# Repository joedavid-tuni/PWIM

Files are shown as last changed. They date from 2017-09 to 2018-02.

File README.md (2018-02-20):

## ELECTRONIC CONTROL OF HYRDRAULIC SYSTEMS

## Description of the Task

As mobile equipment becomes more technologically sophisticated, the need for electronic control of
hydraulic systems is growing.

Electronic components have become more reliable and rugged. They can now withstand the harsh
environmental conditions required for mobile equipment applications. Sophisticated electronic
controllers normally supply only low power control signals.

The goal of the project is to build an electronic driver circuit that compensates the stiction and
hysteresis of a hydraulic valve that makes their behaviour seem erratic and unpredictable. Once we
get over these issues we move on to implement a current sensing mechanism by which the current
in the solenoid circuit is prevented from fluctuating due to varying resistance from varying
temperatures of the coil. We as such are not interested in the position of the spool at any given
point in time but rather only to regulate the current.

## Table of Contents

- Terms of Reference
- Abstract
- Acknowledgement
- 1. Introduction
   - 1.1 Hydraulic Valve
      - 1.1.1 Introduction
      - 1.1.2 Working Principle
      - 1.1.3 Solenoid
      - 1.1.4 Characteristics of Solenoid Coil
   - 1.2 Methods for Proportional Control
      - 1.2.1 Using a potentiometer in Series with the Solenoid
      - 1.2.2 Pulse Width Modulation
      - 1.2.3 Problems associated with Proportional Control of Solenoids
   - 1.3 Solutions to Problems associated with Proportional Control – The Concept of Dither
      - 1.3.1 High frequency PWM
      - 1.3.2 Low frequency PWM
      - 1.3.3 Superimposing Low Frequency Dither on High Frequency Signal
- 2. Current Sensing
   - 2.1 INA219
   - 2.2 PID Algorithm
- 3. Project Work
   - 3.1 Major Hardware Components
   - 3.2 Software
      - 3.2.1 Simulation
      - 3.2.2 Programming IDE
      - 3.2.3 PCB Design Software
   - 3.3 Project Implementation
      - 3.3.1 Basic Circuit
      - 3.3.2 Calculating Inductance
      - 3.3.3 Dither
      - 3.3.4 Current Sensing
      - 3.3.5 Making the PCB
- 4. Project Setup
- 5. Conclusion
- 6. Project Resources
- 7. References
- APPENDIX A: I^2 C Communication Protocol
- APPENDIX B: Setting PWM Frequency on Arduino
- APPENDIX C: The PID Algorithm
- APPENDIX D: TROUBLESHOOTING
- Figure 1: Parts of the Hydraulic Valve List of Figures
- Figure 2: Internal cross section of the Hydraulic Valve
- Figure 3: Coil of Solenoid A energized
- Figure 4: Neutral Position of Valve Plunger
- Figure 5: Testing using mechanical override
- Figure 6: Cross-sectional sketch of Solenoid A of hydraulic valve
- Figure 7: Depiction of the magnetic field around solenoid
- Figure 8: Solenoid current characteristics
- Figure 9: Width of pulses at different duty cycles
- Figure 10: Duty cycle with respective current waveform
- Figure 11: A typical hysteresis curve in an electro hydraulic proportional valve
- Figure 12: Dither as a by-product of low frequency PWM
- Figure 13: Low Frequency Dither superimposed on high frequency PWM
- Figure 14: Functional block diagram of commercially available Solenoid Driver
- Figure 15: Dither Generating Circuitry of a commercially available driver
- Figure 16: Software Code for creating Dither
- Figure 17: Functional Block Diagram of INA219 Sensor
- Figure 18: LCD Display used in the project
- Figure 19: Screenshot of Multisim GUI
- Figure 20: Screenshot of Labcenter Proteus GUI
- Figure 21: Screenshot of Arduino IDE GUI
- Figure 22: Screenshot of Autodesk Eagle GUI
- Figure 23: An FET and a freewheeling diode used to drive the solenoid valve.
- Figure 24: Laboratory setup while calculating inductance
- Figure 25: Oscilloscope Screenshot at resonance
- Figure 26: Multisim simulation circuit
- Figure 27: Breadboard schematic
- Figure 28: General Schematic
- Figure 29: Simulated oscilloscope screenshot (Low frequency)
- Figure 30: Project Implementation waveform from the Arduino (Low frequency)
- Figure 31: Simulated oscilloscope screenshot (High frequency)
- Figure 32: Project Implementation waveform from the Arduino (High frequency)
- Figure 33:: Project Implementation of superimposed waveform from the Arduino.
- Figure 34: Breadboard schematic for current sensing
- Figure 35: Project implemented waveform from the Arduino with current sensing incorporated
- Figure 36: Schematic of Printed Circuit Board of Valve Driver Circuit
- Figure 37: Board Layout of Printed Circuit Board of Valve Driver Circuit
- Figure 38: 3D rendered images of designed Printed Circuit Board
- Figure 39: 3D rendered images of designed Printed Circuit Board
- Figure 40: 3D rendered images of designed Printed Circuit Board
- Figure 41: 3D rendered images of designed Printed Circuit Board
- Figure 42: Project Setup

## 1. Introduction

### 1.1 Hydraulic Valve

#### 1.1.1 Introduction

The Hydraulic Valve used for this Project is a bi-directional solenoid valve from BOSCH.

These are designed to perform any of three actions. They direct the flow of fluid in a hydraulic
system in a particular direction. They can halt or initiate the flow of fluid in a system. Directional
valves can also change the direction in which a fluid flows within a circuit. Various directional valves
are incorporated in hydraulic systems to enable proper flow of fluids. Spool valves in particular are
designed to block and allow the flow of fluid within a hydraulic system.

Parts of the Hydraulic Valve (as labelled in Figure 1)

1. 3 port/chamber system with spool guidance
2. Pressure tight solenoid
3. Optimized flow paths
4. Manual override with return spring

#### Figure 1 : Parts of the Hydraulic Valve

<a href="https://drive.google.com/uc?export=view&id=103Zk_Gb4QrChb2lCu6mXjAdsSugn9ifj">Click for the larger version.</a>

#### 1.1.2 Working Principle

#### Figure 2: Internal cross section of the Hydraulic Valve

<a href="https://drive.google.com/uc?export=view&id=1MhIU9a9HzgaAY-1frNQojasQYRDYau8C">Click for the larger version.</a>

The valve contains two coils on its either end and together with the valve tube that contains an  armature and a push pin make up what is known as a solenoid.

In the main body of the valve there are two springs that help return the spool when no solenoids are
energized. The lines with the gauges labelled A and B are the work ports that typically connect to a
hydraulic cylinder or a motor.

When Solenoid A of the valve is energized an electromagnetic field is created (Figure1). The field
pulls the armature in towards the centre of the winding which causes the armature to slide easily in
a tube that is internally lubricated with hydraulic oil. The armature moves the push pin and
ultimately the push pin moves the valve spool towards the right and now there will be a flow from
the pump directed to work port B. Likewise when Solenoid B is energized, the spool moves to the
left.

#### Figure 3: Coil of Solenoid A energized

<a href="https://drive.google.com/uc?export=view&id=1noz2zwyRv9kF4yIksqgTtab-pTfS3ick">Click for the larger version.</a>

Notice that when Solenoid A is energised the movement of the spool towards the right also causes
the pushpin and armature in Solenoid B is pushed to the right as well.

Also notice that in Figure 2 there is a gap present between the pushpin on the left side of the spool.
When Solenoid A is energized the armature and the push pin gets a running start against the spool
as the gap is closed.

When the solenoid returns to the neutral position after Solenoid A is energized the gap is present
with the Solenoid B. Whichever side of the valve has the pushpin gap has a slight force advantage
when that Solenoid is next energized (Figure 4 ).

#### Figure 4: Neutral Position of Valve Plunger

<a href="https://drive.google.com/uc?export=view&id=1vX9gAe1uKFn87bVOUZPevz9T227o3frZ">Click for the larger version.</a>

In order to help with troubleshooting and basic valve testing, the valve is provided with a mechanical
override (Figure 5), A mechanical override is simply a pin on the outside end of the valve tube in the
centre of the solenoid assembly that can be activated with a small screwdriver or hex key. Pushing
on the mechanical override is a simple way to find out if the internal parts of the valve is still free to
move and operating normally.

#### Figure 5: Testing using mechanical override

<a href="https://drive.google.com/uc?export=view&id=1xGuQGBYz5f1ClA1LN9TVYjQGVeLfPqYV">Click for the larger version.</a>

#### 1.1.3 Solenoid

The hydraulic solenoid valve as mentioned has two solenoids as actuators mounted on either ends
of the valve body. These linear solenoids are electromechanical devices which convert electrical
energy into a linear mechanical motion which is used to control the hydraulic system.
Figure 6 shows a cross sectional sketch of the electromagnetic solenoid hydraulic valve. The
solenoids consist of an electromagnetically inductive coil wound around a movable armature, or
plunger. The coil is shaped such that the armature can be moved in and out of its centre, altering the
coil’s inductance. The plunger provides mechanical force to activate the control mechanism, for
example opening and closing of a valve.

#### Figure 6: Cross-sectional sketch of Solenoid A of hydraulic valve

<a href="https://drive.google.com/uc?export=view&id=1pHDuV0NiXC4nKBy8d_73bMfwTTyaZYxM">Click for the larger version.</a>

#### 1.1.4 Characteristics of Solenoid Coil

A main electrical characteristic of a solenoid is that of an inductor that opposes any change in
current. This characteristic is why current does not immediately reach a maximum level when a
solenoid is energized. Instead, the current rises at a steady rate until it is limited by the DC resistance
of the solenoid.

#### Figure 7: Depiction of the magnetic field around solenoid

<a href="https://drive.google.com/uc?export=view&id=10Lr9DRpki1RoA1x1QTP7i0Ylmb1DseCf">Click for the larger version.</a>

An inductor (in this case a solenoid) stores energy in the form of a concentrated magnetic field.
Whenever current is present in a wire or conductor, a magnetic field, however small, is created
around the wire. With the wire wound into a coil, such as in the solenoid, the magnetic field
becomes very concentrated. This electromagnet can control a mechanical valve through an electrical
signal.

As soon as the solenoid is energized, the current increases, causing the magnetic field to expand
until it becomes strong enough to move the armature and the corresponding solenoid current is
known as IPEAK.

#### Figure 8: Solenoid current characteristics

<a href="https://drive.google.com/uc?export=view&id=1ldvCfLj_Tx2C3A3EPOGBCEJUdh6es91O">Click for the larger version.</a>

The armature movement increases the concentration of the magnetic field as the armature’s own
magnetic mass moves farther into the magnetic field. Remember, a magnetic field changing in the
same direction of the current creating it induces an opposing voltage into the windings. Because the
magnetic field quickly expands when the armature strokes, the field causes a brief reduction in the
current through the solenoid windings till a minimum known as IVALLEY (Figure 8). Notice the
prominent dip in the rising portion of the current waveform.

After the armature strokes, the current continues on its normal upward path to its maximum level. A
typical current waveform in shown in Figure 8.

### 1.2 Methods for Proportional Control

When voltage is applied to a valve coil, the current flowing through it creates a magnetic field which
provides the force to shift the valve’s spool. The input voltage divided by the resistance of the coil
equals the current draw. This is very straightforward when used with on/off valves, but proportional
valves are only useful if the spool position can be precisely controlled by varying the input current.

#### 1.2.1 Using a potentiometer in Series with the Solenoid

A simple potentiometer can be used to vary the resistance, which then varies the input current. This
is an inefficient method of control, and is not practical when high currents are required. Also, when
an infinitely variable DC signal is used to operate a proportional valve solenoid, the output transistor
functions like a variable resistor. It drops the power supply voltage down to the level required by the
solenoid coil at a particular time. The full coil current, which may be several amps, needs to pass
through this output transistor. The result is that the transistor builds up heat which requires a large
heat sink to dissipate.

#### 1.2.2 Pulse Width Modulation

Pulse Width Modulation (PWM) is a control technique which can overcome the problems described
above. With PWM, the output transistor is used as an on/off switch, feeding the solenoid coil with a
series of on/off pulses at a constant voltage. The pulses are set at a constant frequency, typically 400
to 5000+ Hz. The signal level is determined by varying the duration of the “on” pulses relative to the
“off” pulses.

The advantage of this technique is that during the “off” pulse, the output transistor is not passing
any current, and during the “on” pulse, there is virtually no voltage drop across the transistor and
therefore very little heat is created. In practice, there will be a small voltage drop across the
transistor during the “on” pulses, and it takes a finite amount of time to switch on and off, so a small
amount of heat is created. However, the amount of heat is much smaller than would be produced by
a conventional DC output signal.

PWM has become the standard for all valve amplifiers in order to reduce amplifier size and power
waste. No modifications are required to the valve solenoid in order to use this technique.

PWM is an efficient way to control current to a proportional valve coil. It allows the use of
electronics for current regulation, dither, ramping, short circuit protection, and the elimination of
deadband.

**How PWM Works**

A PWM signal is not constant, it is on for a period of time and off for a period of time (see Figure 9 ).

#### Figure 9: Width of pulses at different duty cycles

<a href="https://drive.google.com/uc?export=view&id=1Hj7wRIMUwGXi5BsZQd7tWuWXpfzszCKg">Click for the larger version.</a>

The duty cycle “D” refers to the “on” portion of the cycle. The duty cycle can be anywhere from 0
(signal always off) to 1 (signal always on). A 50% “D” results in a perfect square wave.

Inductance is the characteristic of a circuit that opposes the starting, stopping or changing of current
flow. Inductance in an electrical system is similar to inertia in a mechanical system. Its effect is to
introduce a time lag into the duty cycle wave form. In theory, the wave form is perfectly rectangular,
rising immediately when current is applied, and falling immediately when current is withdrawn.
Because of the effects of inductance, the actual wave form rises and falls more gradually (see Figure
10 ).

#### Figure 10: Duty cycle with respective current waveform

<a href="https://drive.google.com/uc?export=view&id=1ye-VUofCY1JmQrYZPyqtdv7DvxmzGXA0">Click for the larger version.</a>

At 25% signal, “D” is shorter than the time it takes the current to reach its maximum value. This
results in reduced current output to the valve coil, and therefore a reduced hydraulic output from
the valve. If the PWM frequency is low enough, the current will fall to zero during the off time. This
is described as “discontinuous current.”

#### 1.2.3 Problems associated with Proportional Control of Solenoids

There are two major problems that are associated with basic proportional control of solenoid.

1. Stiction

Stiction keeps the valve spool from moving when input signal changes are small. When the signal
finally becomes large enough to initiate movement, the spool will tend to overshoot the position
required for accurate control.

2. Hysteresis

#### Figure 11: A typical hysteresis curve in an electro hydraulic proportional valve

<a href="https://drive.google.com/uc?export=view&id=1HjYDC2TtLQYjVnxpmJmntj7FKT0Biom-">Click for the larger version.</a>

The spool movement in a proportional valve has to overcome some amount of spring force as well
as static friction when the input signal is applied. These forces produce an effect known as
hysteresis. Additionally, the solenoid has to overcome the magnetic hysteresis due to the cyclic
magnetization and demagnetization of the solenoid core. The spool movement in response to the
increasing input signal is not the same as the spool movement created in response to the decreasing
input signal. Hysteresis as shown in the figure above is defined as the difference in the spool position
produced by a particular input signal when it is increasing and then decreasing.

Stiction and hysteresis can make the behaviour of a hydraulic proportional valve seem erratic and
unpredictable. In the following sections, we will see how to overcome these problems.

### 1.3 Solutions to Problems associated with Proportional Control – The Concept of Dither

Dither is a rapid, small movement of the spool around the desired position. It is intended to keep the
spool moving to avoid stiction and average-out hysteresis. Dither amplitude must be **large enough
and the frequency slow enough for the spool to respond, and yet amplitude small and frequency
fast enough to avoid creating a noticeable pulsation in the hydraulic output of the valve.** Dither is
caused by coil current “ripples”—current variations around the desired control signal value. Due to
inertia, the valve spool will follow low frequency ripples better than it will follow high frequency
ripples. The amplitude of the ripples determines if, or how far, the spool will move at a given
frequency.

#### 1.3.1 High frequency PWM

The solenoid valves are very often operated by means of PWM signals at a frequency that is high for
the solenoid valve, for example at l KHZ, in the linear or analog range. The armature of the solenoid
valve cannot synchronously follow this high control frequency in mechanical terms and assumes an
intermediate position.

#### 1.3.2 Low frequency PWM

Previously these problems Were solved in that the frequency of the control signal has been reduced
to such an extent, for example between 70 - 300 HZ, that the armature can still just about follow and
in the intermediate position or central position is preferably deflected only minimally. This results in
oscillation of the armature, and of the valve connected thereto, about the intermediate position at
low amplitude which is conventionally called dither oscillation (dither signal). This dither oscillation is
desired in principle since the friction resistances at the moving parts of the solenoid valve may be
reduced thereby.

However, it is very difficult to stipulate an optimally constant dither signal amplitude **since the
dither signal depends on the PWM frequency and on the pulse-duty factor (duty cycle)** and
therefore on the coil current flowing in the solenoid valve. With this method, it is therefore **not
possible for the dither signal to form a constant amplitude since the PWM frequency has to be
continuously adjusted as a function of the stipulated desired current value and in the process the
amplitude and the frequency of the dither signal change accordingly.**

#### Figure 12: Dither as a by-product of low frequency PWM

<a href="https://drive.google.com/uc?export=view&id=1ios9JTr9PqKZaDLKV-OdVEeYfnglZrMP">Click for the larger version.</a>

#### 1.3.3 Superimposing Low Frequency Dither on High Frequency Signal

A further solution for said problems consists in a low-frequency dither signal being superimposed on
the high frequency of the PWM signal by amplitude modulation. This allows the user to
**independently control** amplitude and frequency of the **solenoid current** and the **dither**. The dither
will therefore be constant for any current level, and its frequency and amplitude can be set by the
user to optimize the function of the particular hydraulic valve. This will be necessary as different
valves from different manufacturers would have different spool dynamics (inertia due to different
size, for example).

#### Figure 13: Low Frequency Dither superimposed on high frequency PWM

<a href="https://drive.google.com/uc?export=view&id=1-vaZGm2uEeG3nVKuvEL_0PmVU9jZDm8H">Click for the larger version.</a>

The dither is specified by its frequency (Hz) and peak-to-peak current. The dither amplitude is usually
adjustable from 0 to 10% of the rated maximum current of the solenoid.

It is to note that, if the dither frequency is in the range of the control frequency, undesirable low-
frequency beating of the magnetic current can occur. Even the hydraulic system may be damaged
thereby. The beating results because the dither frequency cannot be synchronized with the control
frequency.

**Hardware Techniques**

Most solenoid valve drivers make use of a separate dither generating circuitry and combines it with
the main PWM signal using op-amps. The functional block diagram of one such driver is as shown in
the figure below:

#### Figure 14: Functional block diagram of commercially available Solenoid Driver

<a href="https://drive.google.com/uc?export=view&id=1qd2-SRFe5xwFcBycASi99DSaOHfmeA4B">Click for the larger version.</a>

A dither generating circuit of a commercially available solenoid driver is shown below. This is capable
of generating triangular and square wave dither.

#### Figure 15: Dither Generating Circuitry of a commercially available driver

<a href="https://drive.google.com/uc?export=view&id=1yqVyhJahEJyZMxh-2SUGGK5sMoNQTPDx">Click for the larger version.</a>

Working principle:

The dither generator consists of a comparator stage (A1A), amplitude limiting stages (A1C/D2 AND
A1D/D1) and an integrating amplifier stage (A1B). In the beginning, A1A will attempt to go to
positive or negative saturation. However, the peak voltage will be restricted by D1/A1D or D2/A1C.
A1B ramps up or down, as whatever the case maybe, until the output voltage is sufficient to cause
the feedback voltage at the comparator (through voltage divider R8, R11) to change polarity. At this
point, the polarity of A1A changes and A1B ramp in the opposite direction. This way, the dither
signal is generated.

Solutions of this nature are cost-intensive.

**Software Technique**

For the context of the project, we focus only on
superimposing the dither on main PWM signal. As
such, the requirements are basic and we do not need
sophisticated electronics for the purpose. All the
hardware needed would be the basic hardware for
the PWM switching of the solenoid and the dither can
be implemented without using the dither circuitry buy
by rather manipulating the switching hardware
through the software. This section is a description of
how it is done.

#### Figure 16: Software Code for creating Dither

<a href="https://drive.google.com/uc?export=view&id=17Wmvigc5C_fGLL_dgWxXKkvWKsJW3kRq">Click for the larger version.</a>

Using software, the microcontroller is programmed so that the duty cycle of the PWM is periodically
oscillated about its set setpoint, by the dither amplitude which in “duty-cycle language” is in effect a
small finite amount of pulse-duty factor. This in effect causes an extended and thereafter a
shortened PWM signal cyclically which emulates dither. This way, the pulse-duty factor is changed
by the desired amplitude of the dither signal exactly every consequent cycle.

A constant amplitude for the dither signal may advantageously be formed thereby, so the armature
of the solenoid valve always oscillates about its central position with identical excursions, without
the control frequency of the PWM signal being able to have an adverse effect. The resulting reduced
friction resistance therefore allows the position of the armature to be advantageously adjusted and
controlled much more accurately as discussed earlier

The low frequency of the dither signal means that the oscillation of the solenoid valve armature can
be individually adjusted to the type of solenoid valve being used, so, compared with the known
hardware solution, a high level of flexibility results because the adaptation to other types of solenoid
valve can take place by way of a simple calibration process by changing a value in the code that the
microcontroller uses to generate the dither. It is also cost efficient in terms of the components used
as the dither circuitry is now replaced by software code.

## 2. Current Sensing

As mentioned in the previous section, the armature of a solenoid provides a mechanical force to
activate the control mechanism. The force applied to the armature is proportional to the coil’s
change in inductance with respect to the armature’s change in position. The electromagnetic force
of a solenoid directly relates to the current. Traditionally, a voltage drive powers the solenoid coils;
Therefore, the coil consumes a continuous power. A negative effect of this power consumption is
the heating of the coil. The coil temperature is a result of many factors: ambient temperature, self-
heating due to the coil’s power consumption (V × I), heating induced by the contact system, and
other heat sources such as components in the vicinity of the relay. Due to coil heating, the coil
resistance increases. The resistance at elevated temperature is expressed by Equation:

where

- RCoil_20°C is the 20°C value for resistance
- kR_T is the thermal coefficient of copper (= 0.00404 per °C) (1)

Typically given in the datasheet of a solenoid coil, RCoil_20°C can calculate the worst-case coil
resistance at high temperatures.

To compensate for temperature induced changes, we have to implement some sort of current
sensing algorithm which essentially is a current feedback. This allows the solenoid current to be
proportional to the input signal voltage, and independent of the solenoid resistance. Power supply
voltage must be sufficient to overcome the increased or decreased resistance

### 2.1 INA219

The current sensor used for the project is the INA219.

The two analog inputs to the INA219, IN+ and IN–, connect to a shunt resistor in the bus of interest.
The INA219 is typically powered by a separate supply from 3 to 5.5 V. The INA219 senses the small
op across the shunt for shunt voltage, and senses the voltage with respect to ground from IN– for
the bus voltage. Figure 13 shows this operation

#### Figure 17: Functional Block Diagram of INA219 Sensor

<a href="https://drive.google.com/uc?export=view&id=1i2oJyiAauu5uhqEkzyX2_yDP42nBgh-j">Click for the larger version.</a>

### 2.2 PID Algorithm

The PID Controller is implemented to achieve the current sensing functionality. See APPENDIX C: The
PID Algorithm to see the details of the PID Algorithm.

The PID algorithm consists of three basic coefficients; proportional, integral and derivative which are
varied to get optimal response. The basic idea behind a PID controller is to read the values from the
current sensor, then compute the desired actuator output by calculating proportional, integral, and
derivative responses and summing those three components to compute the output.

**Proportional Response:** The proportional component depends only on the difference between the
set point and the process variable. This difference is referred to as the Error term. The proportional
gain (Kp) determines the ratio of output response to the error signal. Increasing the proportional
gain will increase the speed of the control system response. However, if the proportional gain is too
large, the process variable will begin to oscillate. If Kp is increased further, the oscillations will
become larger and the system will become unstable and may even oscillate out of control.

**Integral Response:** The integral component sums the error term over time. The result is that even a
small error term will cause the integral component to increase slowly. The integral response will
continually increase over time unless the error is zero, so the effect is to drive the Steady-State error
to zero. Steady-State error is the final difference between the process variable and set point. A
phenomenon called integral windup results when integral action saturates a controller without the
controller driving the error signal toward zero.

**Derivative Response:** The derivative component causes the output to decrease if the process
variable is increasing rapidly. The derivative response is proportional to the rate of change of the
process variable. Increasing the derivative time (Td) parameter will cause the control system to react
more strongly to changes in the error term and will increase the speed of the overall control system
response. Most practical control systems use very small derivative time (Td), because the Derivative
Response is highly sensitive to noise in the process variable signal. If the sensor feedback signal is
noisy or if the control loop rate is too slow, the derivative response can make the control system
unstable

**Tuning**

The method used for tuning the PID Controller in this project is the “trial and error” method.

In this method, the I and D terms are set to zero first and the proportional gain is increased until the
output of the loop oscillates. As one increases the proportional gain, the system becomes faster, but
care must be taken not make the system unstable.

Once P has been set to obtain a desired fast response, the integral term is increased to stop the
oscillations. The integral term reduces the steady state error, but increases overshoot. Some amount
of overshoot is always necessary for a fast system so that it could respond to changes immediately.
The integral term is tweaked to achieve a minimal steady state error.

Once the P and I have been set to get the desired fast control system with minimal steady state
error, the derivative term is increased until the loop is acceptably quick to its set point. Increasing
derivative term decreases overshoot and yields higher gain with stability but would cause the system
to be highly sensitive to noise.

## 3. Project Work

### 3.1 Major Hardware Components

<a href="https://drive.google.com/uc?export=view&id=1NwfCsXLhD1eqSOyNHsD_ij0nW3hgjotf">Click for the larger version.</a>

**Arduino**

The Arduino Uno is a microcontroller board based on the
ATmega328. Arduino is an open-source, prototyping
platform. The Arduino Uno has 14 digital input/output
pins (of which 6 can be used as PWM outputs), 6 analog
inputs, a 16 MHz crystal oscillator, a USB connection, a
power jack, an ICSP header, and a reset button. It
contains everything needed to support the
microcontroller; simply connect it to a computer with a
USB cable or power it with a AC-to-DC adapter or battery
to get started.

Features of the Arduino UNO:

- Microcontroller: ATmega328
- Operating Voltage: 5V
- Input Voltage (recommended): 7-12V
- Input Voltage (limits): 6-20V
- Digital I/O Pins: 14 (of which 6 provide PWM output)
- Analog Input Pins: 6
- DC Current per I/O Pin: 40 mA
- DC Current for 3.3V Pin: 50 mA
- Flash Memory: 32 KB of which 0.5 KB used by bootloader
- SRAM: 2 KB (ATmega328)
- EEPROM: 1 KB (ATmega328)

## • Clock Speed: 16 MHz

We use the Arduino to create the appropriate PWM signals for controlling the voltage to the
solenoid and to implement the algorithm for current sensing.

**Bidirectional Hydraulic Vale**

Manufacturer: Bosch Rexroth (BRH)

Part No.: 0810091203

Solenoid Specs:

Rating: 24V, 1.4A

**Power Supply**

Specs:

Rating: 24V,2.5A

**INA219, Bidirectional Current/Power Monitor with I2C Interface**

The INA219 is current shunt and power monitor with and I^2 C
interface. This along with the fact that it could be wired on the high
side were the prime reasons the device was selected to be used with
the I2C compatible Arduino.

The device is capable of monitoring both shunt voltage and the bus
supply voltage. The device uses a 3-5V supply, drawing a maximum of 1 mA of supply current and
operates from -40°C to 125°C.

**16x4 Liquid Crystal Display.**

A 16x4 LCD Display is used to display the circuit parameters such as duty cycle, current, etc. real
time.

The parameters on Display are:

Line 1: Duty cycle (Range: 0- 100 , from setpoint) Voltage: Voltage of the Solenoid Circuit
Line 2: I1 : Current sensed by the I2: Expected Current from duty cycle
current sensor (Feedback for PID)
Line 3: Power: VI Power Dissipated in the Solenoid Circuit
Line 4: PID constants (Kp, Ki, Kd)

#### Figure 18: LCD Display used in the project

<a href="https://drive.google.com/uc?export=view&id=1-ABclzSzZyn64kzNVGeBQozGHO7Giizi">Click for the larger version.</a>

**Other Electrical Components**

<a href="https://drive.google.com/uc?export=view&id=1LpvatdVxXZvamxfx_jg-BhqFKHSA1nNc">Click for the larger version.</a>

```
Device Part No. Rating Quantity Remarks
FET IRF3205PbF VDSS = 55V, ID = 110A (n-Ch) 1 Switching Device
Capacitor .001K 63 100nF 1 Noise Filter
Resistor - 12Ω 1 Current Limiter
Diode 1N5400 3A, Rectifier Diode 1 Freewheeling Diode
Potentiometer/
Joystick
```
- 10KΩ 1 Input to the System

### 3.2 Software

#### 3.2.1 Simulation

National Instruments, Multisim v12.0 (used for simulating electrical characteristics)

#### Figure 19: Screenshot of Multisim GUI

<a href="https://drive.google.com/uc?export=view&id=1yDhkocze4_SoT9yiW1kYx1o0pmJ9QOiR">Click for the larger version.</a>

LabCenter, Proteus 8 (used for simulating arduino microcontroller (with code) with electrical circuit)

#### Figure 20: Screenshot of Labcenter Proteus GUI

<a href="https://drive.google.com/uc?export=view&id=1wienvCHE1-AMao52zff7h7abuAwJmdlY">Click for the larger version.</a>

#### 3.2.2 Programming IDE

##### ARDUINO IDE

#### Figure 21: Screenshot of Arduino IDE GUI

<a href="https://drive.google.com/uc?export=view&id=177bdEXaEHLrz7efpmUK4lLl1IIjE5Dey">Click for the larger version.</a>

#### 3.2.3 PCB Design Software

#### Figure 22: Screenshot of Autodesk Eagle GUI

<a href="https://drive.google.com/uc?export=view&id=1jIhEK4rQlFEAy6yMQ-lyjC428kQFLo-f">Click for the larger version.</a>

### 3.3 Project Implementation

Before the implementation, the circuit needs to be simulated to study the response of the
circuit beforehand so that time is no wasted during implementation stage. An added benefit would
be familiar results and pre-known reasoning during the implementation phase. As mentioned in the
earlier sections we use MultiSim v12.0 and Proteus 8.0 for simulations. Proteus simulations were
made to study the behaviour while designing the project work and its observations are not recorded
here.

#### 3.3.1 Basic Circuit

Driving a solenoid is a rather simple task with very little need for sophisticated electronics. Still, the
basics of inductive load driving must be taken care of if we are to safely actuate this load. These
requisites are:

- A large enough voltage must be applied across the winding in order to supply a current with
    enough magnitude as to push/pull the piston.
- The switch or power stage must be sized according to the dc current we expect to see
    flowing across the solenoid winding.
- An alternate path must be applied to take care of the flowing current once the switching
    element is disabled.

A normal MOSFET requires around 10V applied to the Base pin to fully turn on. Because driving
anything above 5V with an Arduino requires using a level-shifter or amplifier, we use what is called a
logic-level MOSFET (IRF 3205) for direct integration. A logic-level MOSFET can be turned on with a 5v
“logic level” signal, which can be easily interfaced to the Arduino.

If a normal MOSFET with an amplified input from the Arduino is used, care must be taken not to
exceed the maximum gate-to-source voltages. If the limit is exceeded for even a second, it can
destroy the MOSFET, so care should be taken to work within the voltage limits of the MOSFET. The
maximum voltage that can be applied to the gate pin is listed in the datasheet as the “Gate to Source
Voltage” or “Vgs” —this number is usually between 18vdc and 25vdc.

For the IRF 3205 we the maximum Vgs is 20V, so it is safe as the Arduino cannot prover over 5V with
direct integration.

The typical solenoid driver circuit is a single FET transistor with enough current handling capability to
drive the load (IRF 3205), and a freewheeling diode which is forward biased when the FET is
disabled. When the FET is enabled, it sinks all the current needed to polarize the inductor. When the
transistor is disabled, the current flowing through the inductance must be allowed to decay down to
zero. The freewheeling diode is forward biased taking this current and avoiding damage to the
power FET. Figure 1 9 shows the two possible states a solenoid will experience as it is energized

#### Figure 23: An FET and a freewheeling diode used to drive the solenoid valve.

<a href="https://drive.google.com/uc?export=view&id=1sQTFtrDf82s8IXWCDfRFEJ_FRTnlli9v">Click for the larger version.</a>

Note that a H-bridge circuit is not used as it’s not a bistable solenoid where the direction of motion
is according to the magnetic field polarity. Hence the direction of current flow is not relevant and
use of an H-bridge would be an overkill as it would need 4 FETs as opposed to one in this case.

All information required to begin simulations is present except one, the inductance of the solenoid
of the hydraulic valve. This was neither found in the product datasheet nor was available with the
Bosch Customer Service personnel on contacting them. So, a basic test is carried out to approximate
the inductance of the solenoid.

#### 3.3.2 Calculating Inductance

To calculate the inductance, connect the solenoid of the hydraulic valve in parallel with a capacitor
to form a tank circuit. Use a function generator to run a small current through the circuit and an
oscilloscope to view the waveform across the solenoid. Next, sweep the function generator
frequency from its lowest top highest range. In this range, the tank's resonant frequency is where
the oscilloscope registers the largest waveform.

#### Figure 24: Laboratory setup while calculating inductance

<a href="https://drive.google.com/uc?export=view&id=1DbEUsarPM3vBnsaWHENC6-nMKgTmmU00">Click for the larger version.</a>

Resonant Frequency of LC tank circuit is given by the formula:

##### 푓=

##### 1

##### 2 휋√퐿퐶

Equation 1

From the equation 1 the inductance can be found, L, as:

##### 퐿=

##### 1

##### ( 2 휋푓)^2 .퐶

Equation 2

Resonance was found to obtained at around 150Hz using
a capacitor of 10μF.

Substituting in Equation 2, the inductance,

```
L= 0.10554 H or 105.54mH
```
#### 3.3.3 Dither

Now, that the inductance of the solenoid is established, it is simulated in softwares. Next,
simulations at both higher and lower frequencies is carried out and the observations are recorded
below.

**Simulation Circuit**

The circuit built is shown in the figure below.

As can be seen the **voltage across the solenoid is connected to channel A** and **the current in the
solenoid is connected to channel B** of the oscilloscope.

#### Figure 25: Oscilloscope Screenshot at resonance

<a href="https://drive.google.com/uc?export=view&id=1k7YGEA7DGEtcj9yKaFBfLAySiLHO5YZx">Click for the larger version.</a>

#### Figure 26: Multisim simulation circuit

<a href="https://drive.google.com/uc?export=view&id=1Tc4o473i5xGG8D_BdxKo3akBl32X1_w4">Click for the larger version.</a>

**Arduino Valve Driver Circuit**

#### Figure 27: Breadboard schematic

## Figure 28: General Schematic

The PWM frequency on most pins is ~490 Hz. However, it's ~980 Hz for pins 5 and 6 on the Uno. To
obtain lower frequencies a deeper understanding on the hardware implementation of the ATMEL
328p Microprocessor that the Arduino uses is necessary.

See APPENDIX B: Setting PWM Frequency on the Arduino to see how a frequency different from that
of the default frequency was obtained.

Also see APPENDIX D: Troubleshooting to see how to eliminate noises in the analog input

The waveforms from the scope are shown in the figure below.

**Low Frequency Dither Observations**

(refer Section 2.3.2 for literature)

Frequency: ( 60 Hz) and PWM with
duty cycle: 80%

**Simulation Results:**

## Figure 29: Simulated oscilloscope screenshot (Low frequency)

As described in Section 2.3.2, low frequency PWM generates dither (current ripple) as a by-product
of the PWM process. The PWM frequency is low enough so that the current has time to decay
before the next rise begins.

**Project Implementation Results**

## Figure 30: Project Implementation waveform from the Arduino (Low frequency)

The above is a plot of instantaneous values of the current (Y-axis) vs time (x-axis) that that micro-
controller records. The blue is the expected current value at 80% duty cycle whereas the redline is
the current values sensed by the sensor in the feedback circuit. It is observed that the frequency of
the PWM is low enough that it reduces to 0 at moments. This is in line with what was expected and
as shown in the simulations

**Valve Behaviour**

As the duty cycle was increased, the plunger of the solenoid began to vibrate with larger amplitude
and finally actuated. This was as expected as mentioned in the Section 2.3.2. Changing the PWM
frequency will allow adjusting the dither, but the amplitude and frequency of the dither cannot be
set independently.

**Results from Test Bench.**

Due to large hysteresis of the solenoid used in the test bench, the dither could be observed in the
initial stages for a brief amount of time but it quickly actuated.

**High Frequency Dither Observations**

(refer Section 2.3.1 for literature)

**Simulation Results:**

Frequency: ( 490 Hz – Arduino Default frequency) and PWM with
duty cycle: 80%

## Figure 31: Simulated oscilloscope screenshot (High frequency)

Here, it is clear that the frequency of the PWM signal is high enough that it does not let the current
to a minimum zero value.

**Valve Behaviour**

The armature of the solenoid valve cannot synchronously follow the current in mechanical terms
and assumes an intermediate position. With a pulse duty factor of 50% of the PWM signal this then
corresponds to the central position of the valve “half open”. But this as discussed in Section 2 .3.1
will be subject to problems of stiction and thereby hysteresis due to lack of dither oscillation.

**Project Implementation Results**

There were no significant dither observations, as expected. The high frequency did not allow the
plunger dither oscillations.

## Figure 32: Project Implementation waveform from the Arduino (High frequency)

The blue is the expected current value at 80% duty cycle whereas the redline is the current values
sensed by the sensor in the feedback circuit. The frequency of the PWM is high enough to produce a
continuous current.

```
-- Input
-- Setpoint
```

**Superimposing Low Frequency Dither on High Frequency Signal**

(refer Section 2.3.3 for literature)

This is obtained in the software implementation by periodically varying the duty cycle.

**The PWM frequency runs at a high frequency, while
the duty cycle oscillation along with a delay in
between produces the effect of low frequency dither.**

**Valve behaviour**

This causes just enough oscillation of the solenoid
plunger, not to keep it stationary as well not to
produce considerable variation in the plunger
displacement.

## Figure 33:: Project Implementation of superimposed waveform from the Arduino.

Here the “dither_time” variable is set to 10ms so 1 complete cycle of the dither wave takes
approximately 20ms. Hence the **dither frequency is 50Hz**

The blue is the expected current value at 80% duty cycle whereas the redline is the current values
sensed by the sensor in the feedback circuit.

At the moment, there isn’t any feedback which is why there is considerable steady state error.

```
-- Input
-- Setpoint
```

#### 3.3.4 Current Sensing

**Introduction**

Here the objective is to implement a PID algorithm, that inputs feedback from a current sensor. As
discussed in Section 3 the objective is to make sure that for a given setpoint from the input joystick,
the output must be the same at all times, irrespective of the varying ambient temperature due
varying weather conditions

**Circuit Diagram**

The circuit is rigged up as per the following diagram,

```
Current sensing
```
## Figure 34: Breadboard schematic for current sensing

**Software Code**

The code begins with the necessary pre-processor directives. They are invoked by the compiler to
process the class definitions before compilation.

Next, initialize objects of these classes, to use them throughout the code.

Initialize Variables for use

Setup Function, that runs once when the Arduino runs the program.

The setup function is used to setup the parameters of the instances of class objects initialized earlier.
This includes the LCD, PID, Current Sensor and the Arduino GPIO Pins.

**Loop Function**

This function is the main function and runs every cycle continuously

See APPENDIX D: Troubleshooting to set a PWM frequency on the fly with carrying setpoint.

**PID Tuning**

See APPENDIX C: The PID Algorithm to see the details of the PID Algorithm.

The procedures taken during tuning were as discussed in Section 3.2.

On starting the tuning the proportional constant the oscillations were already high. Hence it was
decided to keep the Kp parameter near zero or zero. The parameters suitable for the project were
found to be **Kp = 0, Ki = 10 and Kd=0.**

**Project Implementation Results**

## Figure 35: Project implemented waveform from the Arduino with current sensing incorporated

It can be observed that as the duty cycle of the PWM output is varied (blue line), output (green line)
varies almost instantaneously so that the input (current in the solenoid coil) closely follows the
setpoint.

When the current in the solenoid of the hydraulic valve reduces due to the increase in the resistance
the PID controller automatically adjusts the output to achieve the desired current level.

```
-- Output
-- Input
-- Setpoint
```

#### 3.3.5 Making the PCB

Once the objectives of the project have been achieved, it is made permanent by transferring the
breadboard to a Printed Circuit Board.

The software Eagle, from Autodesk is used for the purpose to sketch the PCB.

Features of the PCB

1. Besides the circuit already discussed, an additional power circuit is added that is used to
    power the PCB and provide power to the INA219 sensor. It provides a regulated output of 5V
    (4.8V-5.2V) from an external input voltage (5V-18V) through a DC Barrel Connector (2.1mm
    centre positive).
2. 4 Pairs of 5V power supply headers are provided to power auxiliary devices such as an LCD
    or a variable analog input such as a potentiometer or a joystick. Please note that the current
    sensor is powered from within the PCB and a separate connection is not required.

**Schematic:**

## Figure 36: Schematic of Printed Circuit Board of Valve Driver Circuit

**Board View:**

## Figure 37: Board Layout of Printed Circuit Board of Valve Driver Circuit

##### 43

**Rendering**

## Figure 38: 3D rendered images of designed Printed Circuit Board

## Figure 39: 3D rendered images of designed Printed Circuit Board

## 4. Project Setup

## Figure 42: Project Setup

## 5. Conclusion

The report starts with literature discussing certain important aspects in the electronic control of
hydraulic systems.

Next, the solenoid valve used in the project was characterised by conducting basic tests on it initially
to determine its inductance as it was not provided in the accompanying datasheet. This information
was used to simulate models in softwares Multisim and Proteus to study the Low Frequency and
High Frequency PWM response with reference to the topics discussed in the literature. Its behaviour
during the simulations were studied and a temporary test circuit was built on a breadboard and the
implementation results were compared with that of the simulation.

A software based technique for determining a control signal for a solenoid valve is next discussed,
the control signal being a PWM signal on which a frequency of a dither signal is superimposed and
having a frequency such that the spool of the solenoid valve assumes an intermediate position
between which the armature oscillates with slight excursions at the frequency of the dither signal.

Upon successful implementation of dither, a current sensing circuit was built using a fine tuned PID
algorithm. Finally, after running successful tests, a PCB for the prototype was designed.

## 6. Project Resources

All the files used in this project develop are available online at the GitHub repositories with links
given below.

Arduino Sketch: https://github.com/joedavid91/PWIM/tree/master/Arduino%20Code/PWIM

Simulation Files: https://github.com/joedavid91/PWIM/tree/master/Simulation%20Files

Fritzing Sketches: https://github.com/joedavid91/PWIM/tree/master/Fritzing%20Sketches

Eagle PCB Files: https://github.com/joedavid91/PWIM/tree/master/Eagle%20PCB%20Files

Links to Videos:

Low Frequency Dither: https://youtu.be/j71BZkSpgNY

Laboratory Setup with current sensing: https://youtu.be/wHQWNnsTs0Q

Real time PID Plot with current sensing: https://youtu.be/J_p4m4B9xHs

## 7. References

##### [1] “ ELECTRONIC CONTROL OF HYDRAULIC SYSTEMS”

[http://www.hydraforce.com](http://www.hydraforce.com)

##### [2] “FLOW AND DIRECTIONAL CONTROL VALVES”

[http://www.lunchboxsessions.com](http://www.lunchboxsessions.com)

[3] _“Detection of Plunger Movement in DC Solenoids”_ Manu Balakrishnan, Navaneeth Kumar N
Texas Instruments

[4] _“Method and Device for determining a PWM Signal on which a dither frequency is
superimposed in order to control a solenoid” Jose Cruz Kissler Fernandez, Thomas Rohrl_

[5] _“Driving solenoid coils efficiently in switchgear applications_ ” Sanjay Pithadia, Texas
Instruments

[6] “ _Arduino Robotics”_ John-David Warren, Josh Adams and Harald Molle

[7] “ _Secrets of Arduino PWM”_ Ken Shirriff’s blog

## APPENDIX A: I^2 C Communication Protocol

The INA219 offers compatibility with both I2C and SMBus interfaces of which the I2C will be used as
it is compatible with the Arduino. Two bidirectional lines, SCL and SDA, connect the INA219 to the
bus. Both SCL and SDA are open-drain connections meaning that they can pull the corresponding
signal line low, but cannot drive it high. Thus, there can be no bus contention where one device is
trying to drive the line high while another tries to pull it low, eliminating the potential for damage to
the drivers or excessive power dissipation in the system. Each signal line has a pull-up resistor on it,
to restore the signal to high when no device is asserting it low.

The device that initiates the transfer, the Arduino, is called a master, and the devices controlled by
the master are slaves. The Arduino generates the serial clock (SCL), controls the bus access, and
generates START and STOP conditions.

Messages are broken up into two types of frame: an address frame, where the master indicates the
slave to which the message is being sent, and one or more data frames, which are 8-bit data
messages passed from master to slave or vice versa. Data is placed on the SDA line after SCL goes
low, and is sampled after the SCL line goes high. The time between clock edge and data read/write is
defined by the devices on the bus and will vary from chip to chip.

Start Condition

To initiate the address frame, the master device leaves SCL high and pulls SDA low. This puts all slave
devices on notice that a transmission is about to start. If two master devices wish to take ownership
of the bus at one time, whichever device pulls SDA low first wins the race and gains control of the
bus.

Address Frame

The address frame is always first in any new communication sequence. For a 7-bit address, the
address is clocked out most significant bit (MSB) first, followed by a R/W bit indicating whether this
is a read (1) or write (0) operation.

The 9th bit of the frame is the NACK/ACK bit. This is the case for all frames (data or address). Once
the first 8 bits of the frame are sent, the receiving device is given control over SDA. If the receiving
device does not pull the SDA line low before the 9th clock pulse, it can be inferred that the receiving
device either did not receive the data or did not know how to parse the message. In that case, the
exchange halts, and it’s up to the master of the system to decide how to proceed.

Data Frames

After the address frame has been sent, data can begin being transmitted. The master will simply
continue generating clock pulses at a regular interval, and the data will be placed on SDA by either
the master or the slave, depending on whether the R/W bit indicated a read or write operation. The
number of data frames is arbitrary, and most slave devices will auto-increment the internal register,
meaning that subsequent reads or writes will come from the next register in line.

Stop condition

Once all the data frames have been sent, the master will generate a stop condition. Stop conditions
are defined by a 0->1 (low to high) transition on SDA after a 0 - >1 transition on SCL, with SCL
remaining high. During normal data writing operation, the value on SDA should not change when SCL
is high, to avoid false stop conditions.

## APPENDIX B: Setting PWM Frequency on Arduino.......................................................................

The idea here is not to provide a detailed overview of how the processor manages the register, but
only to provide enough information to understand the code in the context of the project.

The ATmega328P has three timers known as Timer 0, Timer 1, and Timer 2. Each timer has two
outputs compare registers that control the PWM width for the timer's two outputs: when the timer
reaches the compare register value, the corresponding output is toggled. The two outputs for each
timer will normally have the same frequency, but can have different duty cycles (depending on the
respective output compare register).

Each of the timers has a prescaler that generates the timer clock by dividing the system clock by a
prescale factor such as 1, 8, 64, 256, or 1024. The Arduino has a system clock of 16MHz and the
timer clock frequency will be the system clock frequency divided by the prescale factor. Note that
Timer 2 has a different set of prescale values from the other timers.

The timers are complicated by several different modes. The main PWM modes are "Fast PWM" and
"Phase-correct PWM" of which the Fast PWM will be used and is described below

Let’s take Timer 1 for example

The Timer/Counter Control Registers TCCR1A and TCCR1B hold the main control bits for the timer.
(Note that TCCR1A and TCCR1B do not correspond to the outputs A and B.) These registers hold
several groups of bits:

- Waveform Generation Mode bits (WGM): these control the overall mode of the timer.

(These bits are split between TCCR1A and TCCR1B.)

- Clock Select bits (CS): these control the clock prescaler
- Compare Match Output A Mode bits (COM1A): these enable/disable/invert output A
- Compare Match Output B Mode bits (COM1B): these enable/disable/invert output B

The Output Compare Registers OCR1A and OCR1B set the levels at which outputs A and B will be
affected. When the timer value matches the register value, the corresponding output will be
modified as specified by the mode.

**Base frequencies:**

The base frequency for pins 3, 9, 10, and 11 is 31250 Hz.

The base frequency for pins 5 and 6 is 62500 Hz.

**Divisors:**

The divisors available on pins 5, 6, 9 and 10 are: 1, 8, 64, 256, and 1024 which are selected by the
mode values and are in hexadecimal format.

The divisors available on pins 3 and 11 are: 1, 8, 32, 64,128, 256, and 1024 which are selected by the
mode values and are in hexadecimal format.

PWM frequencies are tied together in pairs of pins. If one in a pair is changed, the other is also
changed to match:

Pins 5 and 6 are paired on timer0

Pins 9 and 10 are paired on timer1

Pins 3 and 11 are paired on timer2

Below is a code for a function that accepts the Arduino output pin number and the divisor as
arguments which it uses to attain varying frequencies on the Arduino (UNO)

The resulting frequency is equal to the base frequency divided by the given divisor:

## APPENDIX C: The PID Algorithm

Please note that sections of the code that are irrelevant, of negligible importance or self-explanatory
are omitted to keep this section concise.

**The PID class Constructor**

The PID class constructor is used to intialize an instance / obect of the class PID. All the information
regarding the PID object are to be passed as parameters to the constructor. The Input, Output and
the Setpoint variables are pointers, and a reference to these pointer variables are usedwhile creating
the class object as shown below :

The constructor is also used to assign the PID tuning parameters Kp,Ki and Kd using the SetTunings
function (shown in code above). The **step time** is set to **0.1s or 100ms**

The SetOutputLimits function sets the maximum outout of the PID controller. This is necessary as its
intended to control the PWM ouptut of the arduino which is in the range 0-255 as its 8-bit. Without
this function the PID would increase the output beyond 255 and there would be an overflow as the
PWM value is only 8bit.

Lines 67 - 69 of the compute funciton ( code in next page ) ensure that the PID is called only at a
regular interval, based on a **predetermined step time, i.e 100ms**. Once the PID is evaluated at a
constant interval, the derivative and integral calculations can also be simpligfied. As a result of this,
the SampleTimeInSec variable appears in the SetTunings function (code in previous page), which are
multiplied or divided while setting the tuning parameters itself. because it is now known that it’s
going to be the same time between samples,it is unecessary to constantly multiply by time change
which is why time doesn’t appear in the setTunings function. The result is mathematically
equivalent, but more efficient as it saves a multiplication and a division every time the PID is
evaluated

**Compute Function.**

This is where the all the PID computation takes place.

This function should be called every time "void loop()" function of the arduino executes. the
function will decide for itself whether a new pid Output needs to be computed, i.e whether the time
since the previous computation is greater than the constant sample interval defined in the
constructor. It returns true when the output is computed, false when nothing has been done.

**Lines 71- 74** Computes the working error variables.

**Lines 76 and 77** Clamps the Output to its maximum (255) and minimum (0) values respectievely and
make sure there is no over flow.

**Lines 8 0 - 82** , computes the proportional on error output term and adds it to the Final Output on
**lines 8 5**

**Lines 9 7 - 89** , clamps the output to either the maximum or mimnimum values as earlier. This is
necessary to be taken care of at each stage as the variables in the arduino code are referenced as
pointers and any momentary overflow of the PWM register bits can adversely affect the stability of
the system.

**Lines 92 & 93** are used to store the current input time for use in the next computation cycle.

## APPENDIX D: TROUBLESHOOTING

This Section presents few challenges that were faced during the project implementation and how
they were overcome.

**Heating of the MOSFET**

MOSFETs have tiny capacitors attached to their gate pins to maintain the voltage present at the
gate. The capacitor charge enables the MOSFET to stay activated, even after the power is removed
from the gate pin. Each time the MOSFET is switched, the gate capacitor must fully charge and
discharge its current.

As the PWM frequency that is applied to the MOSFET switch increases, the time allowed for the gate
capacitor to charge and discharge decreases. As this happens, the gate-capacitor will require more
current from the driver to fully charge and discharge in the shorter amount of time. If the current
available from the driver is not sufficient to fully charge and discharge between switching cycles, the
gate will be left in a partially conducting state, which can result in excess heating.

Saying that a MOSFET needs a lot of available current to switch quickly might seem puzzling, because
MOSFETs require a specific voltage to turn on and typically very little current. Although the 40mA
that the Arduino PWM output pin can supply is plenty of current to fully switch a MOSFET on or off
slowly, it is not enough to fully charge and discharge the MOSFETs gate-capacitor at high PWM
frequencies where the MOSFET capacitor needs to be fully charged and drained 10,000 (10Khz) to
32,000 (32Khz) times per second!

A solution to this would be using a MOSFET driver IC (specialized signal-buffer) drive the MOSFET
switch because it can provide much more current during each switching cycle than the Arduino is
capable of.

It is also a good idea to ensure that the gate is forced to its off state by using a “pull-down” resistor
to drain the capacitor when not actively powered by the Arduino. Using a 10kOhm pull-down
resistor from the gate pin to the source pin (gate to GND on n-channel, gate to VCC on p-channel)
will be sufficient to keep the MOSFET turned off when not in use.

**Having different frequencies at different duty cycles on the fly**

The code used in the project section sets the main PWM (not dither) of the Arduino in the setup function
and remains the same throughout the execution of the program. Sometimes it may be required that this
PWM signal be changed on the fly with different PWM frequencies at different setpoints. This may be
due an increased stiction at some point or strange hysteresis patterns obtained during the spool
movement. It might be unwieldy to call the setPwmFrequency() method every time this needs to be
done. Rather a more efficient method is presented below.

Here Timer1 is used, which is 16bit, and allows for a number to be stored in a register (ICR1), and the
frequency is calculated based on that number. This gives me outputs on pins 9 and 10.
The number can be any value from 0 – 65535 (size = 16 bits).
The output frequency is given by the formula:

```
표푢푡푝푢푡 푓푟푒푞푢푒푛푐푦=
```
##### 푓

##### 2 푥푁푥푇푂푃

Where f = main clock (16MHz)
N = pre-scalar (see APPENDIX B)

TOP = the value in ICR 1
Based on the values of ICR1 from 1 to 65535 we get a frequency range from 15Hz to 1MHz.
So for example:
ICR1 = 10,000 gives f = 100Hz
ICR1 = 5000 gives f = 200Hz
ICR1 = 2500 gives f = 500Hz and so on..

To do this, the timer is configured to run in phase and frequency correct mode, and can set it to
either inverting or non-inverting mode. The pre-scalar should also be selected.

These configurations are done by adjusting Timer1 registers TCCR1A and TCCR1B.

First thing to adjust is choosing Phase and Frequency correct mode in invert or non-invert mode.

Second thing to adjust is PWM, Phase and Frequency correct mode, with the TOP value determined
by the ICR1 register, which is what determines the PWM Frequency.

The last thing to do is to adjust the pre-scalar.

This is done by choosing the right modes from the above table. As discussed earlier, we shall be
using mode which divides the main clock by 8.

**Smoothing Arduino Analog Input**

While reading the analog input from the joystick or potentiometer it is most likely that the input
behaves like the red line in the below picture. This also partially applies to the analog input of the
feedback sensor

As can be seen, if the fluctuating setpoint drives the PID algorithm crazy. First of all, it’s imperative to
check whether the Arduino and the rest of the circuit have a common ground. This is necessary. A
couple of additional measures were taken to fix this problem

1. Adding a filter capacitor from the analog input pin to ground as shown in Figure 27

2. Using an averaging algorithm. In this project, a basic averaging algorithm is used using a for-
    loop as it was found to suffice. There are however there are more robust algorithms such as
    the moving average or weighted average, the exponential moving average etc.

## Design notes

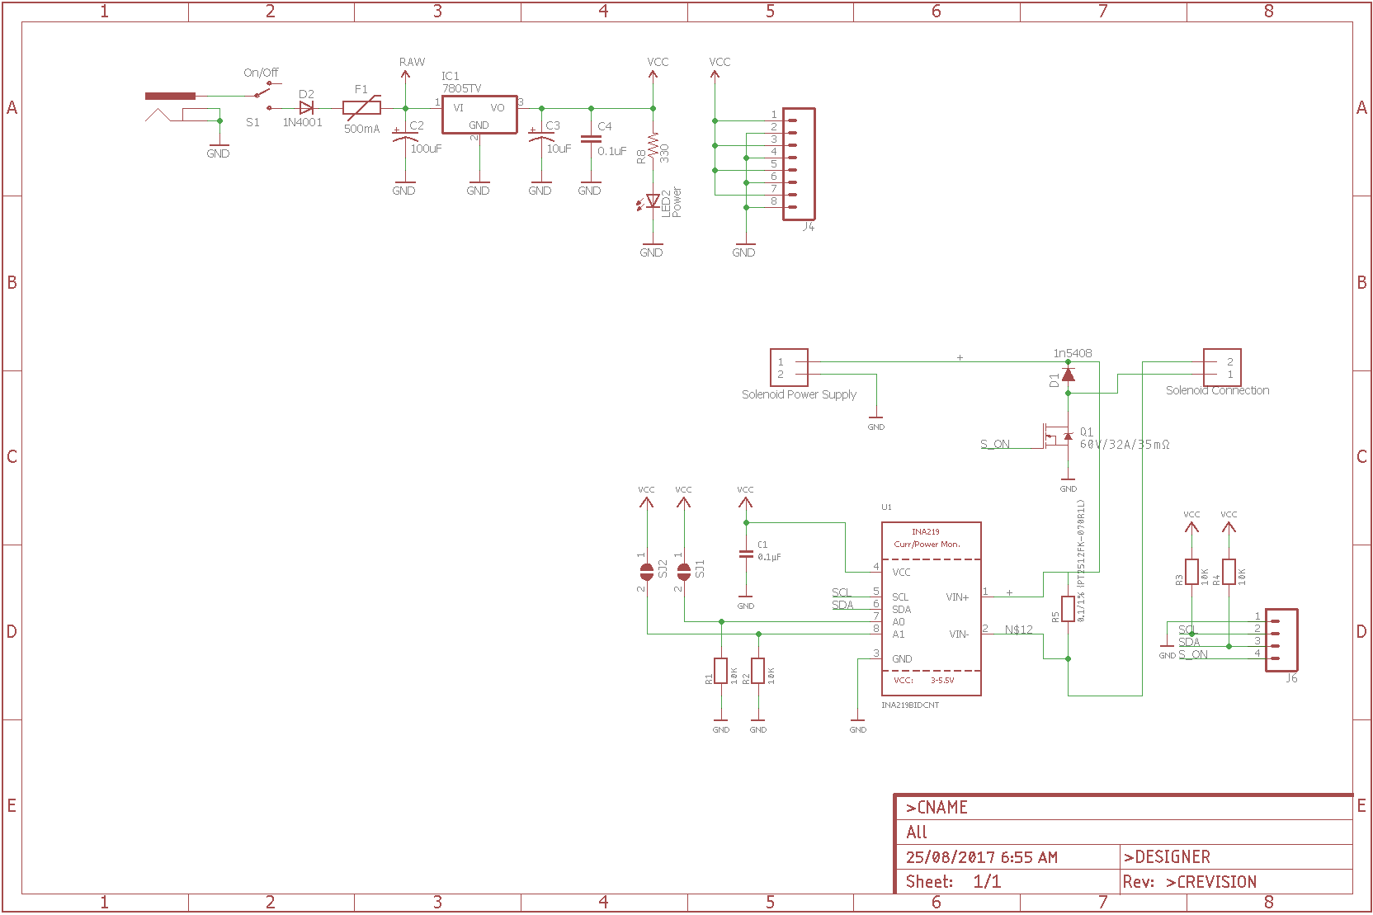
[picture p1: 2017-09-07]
Eagle PCB Files/IN219_breakout/schVer2.png

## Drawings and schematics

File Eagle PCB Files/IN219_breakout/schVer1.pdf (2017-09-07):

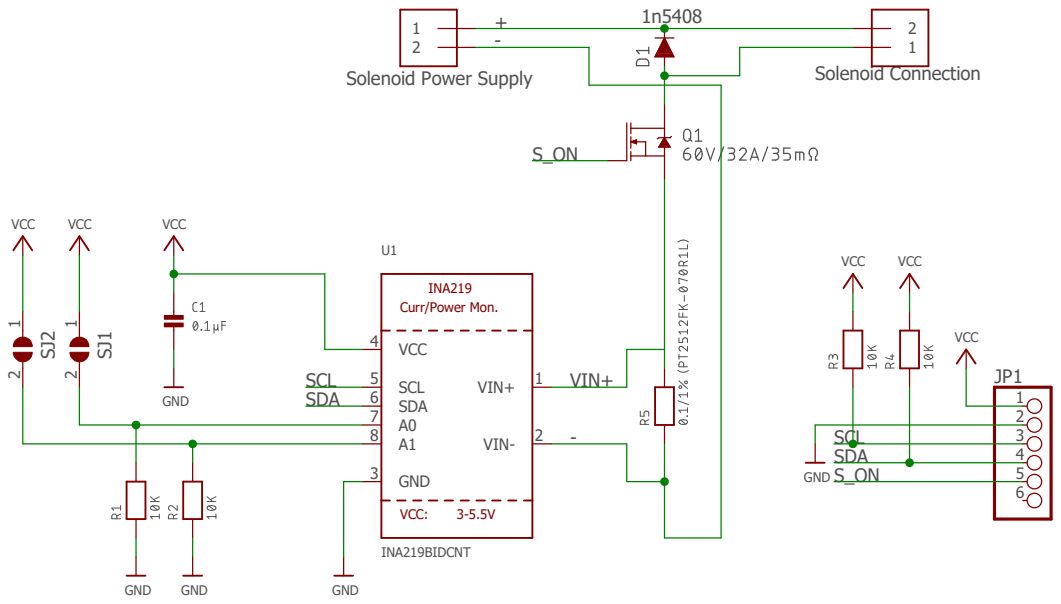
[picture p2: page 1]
VCC; GND; VCC Solenoid Power Supply; Solenoid Connection; INA219BIDCNT; VIN+; VIN-; GND 3; VCC 4; SDA 6; SCL 5; SDA; SCL; INA219 Curr/Power Mon.; VCC:

13/08/2017 2:26 PM C:\Users\Chathuranga\Documents\eagle\IN219_breakout\All.sch (Sheet: 1/1)

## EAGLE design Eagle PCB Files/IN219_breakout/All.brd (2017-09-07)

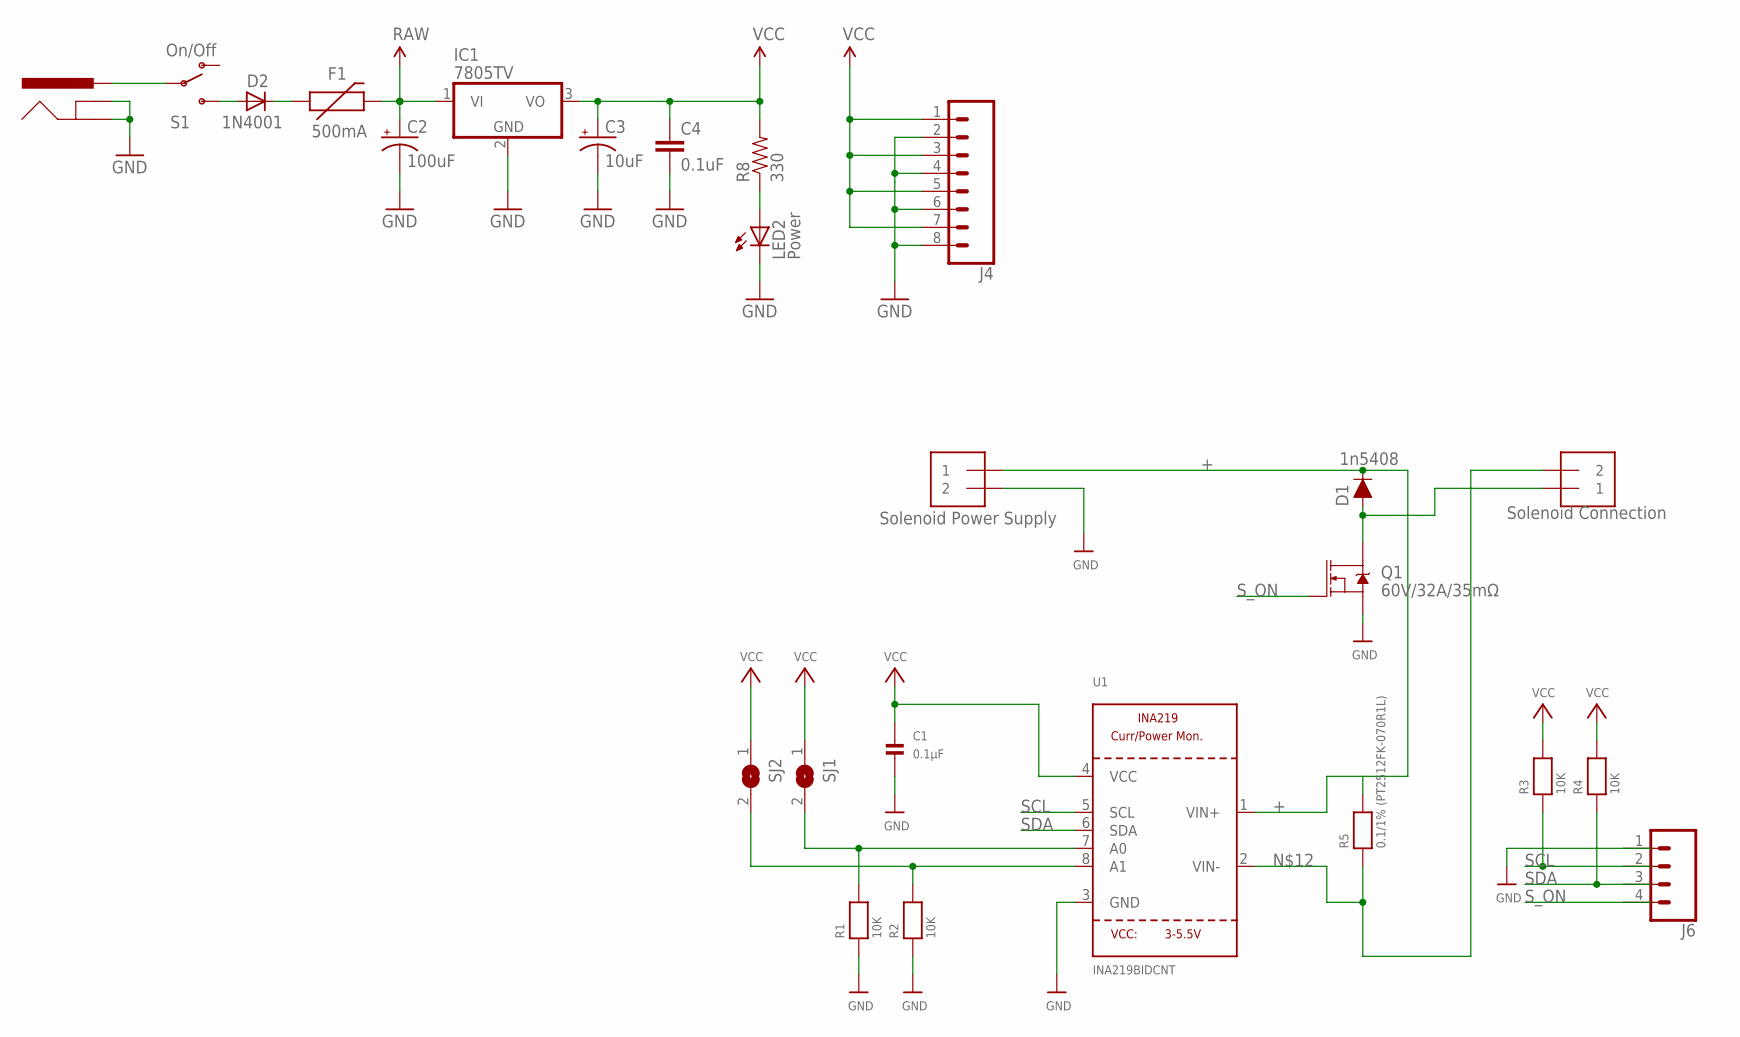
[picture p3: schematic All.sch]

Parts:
C1: 0.1µF; 0805
C2: 100uF; CPOL-RADIAL-100UF-25V
C3: 10uF; CPOL-RADIAL-10UF-25V
C4: 0.1uF; CAP-PTH-SMALL2
D1: DIODE-1N4148
D2: 1N4001; DIODE-0.4
F1: 500mA; PTC
IC1: 7805TV; TO220V
J1: POWER_JACKPTH; POWER_JACK_PTH
J2, J3: TERMBLOCK_1X2-3.5MM; 1X2-3.5MM
J4: CONN_08"; 1X08
J6: CONN_04; 1X04
LED2: Power; LED5MM
Q1: 60V/32A/35mΩ; TO220V
R1, R2, R3, R4: 10K; 0805
R5: 0.1/1% (PT2512FK-070R1L); 2512
R8: 330; AXIAL-0.3
S1: On/Off; SWITCH-SPST
SJ1, SJ2: SOLDERJUMPERREFLOW_NOPASTE; SOLDERJUMPER_REFLOW_NOPASTE
U1: INA219BIDCNT; SOT23-8

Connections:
+: D1.C, J2.1, R5.2, U1.1 (VIN+)
GND: C1.2, C2.2 (-), C3.2 (-), C4.2, IC1.2 (GND), J1.GND, J1.GNDBREAK, J2.2, J4.2, J4.4, J4.6, J4.8, J6.1, LED2.K (C), Q1.3 (S), R1.1, R2.1, U1.3 (GND)
unnamed: R2.2, SJ2.2, U1.8 (A1)
unnamed: R1.2, SJ1.2, U1.7 (A0)
unnamed: D1.A, J3.1, Q1.2 (D)
unnamed: J1.PWR, S1.2
unnamed: LED2.A, R8.P$1 (1)
unnamed: D2.C, F1.P$1 (1)
unnamed: D2.A, S1.3 (S)
unnamed: J3.2, R5.1, U1.2 (VIN-)
RAW: C2.1 (+), F1.P$2 (2), IC1.1 (VI)
SCL: J6.2, R3.1, U1.5 (SCL)
SDA: J6.3, R4.1, U1.6 (SDA)
S_ON: J6.4, Q1.1 (G)
VCC: C1.1, C3.1 (+), C4.1, IC1.3 (VO), J4.1, J4.3, J4.5, J4.7, R3.2, R4.2, R8.P$2 (2), SJ1.1, SJ2.1, U1.4 (VCC)

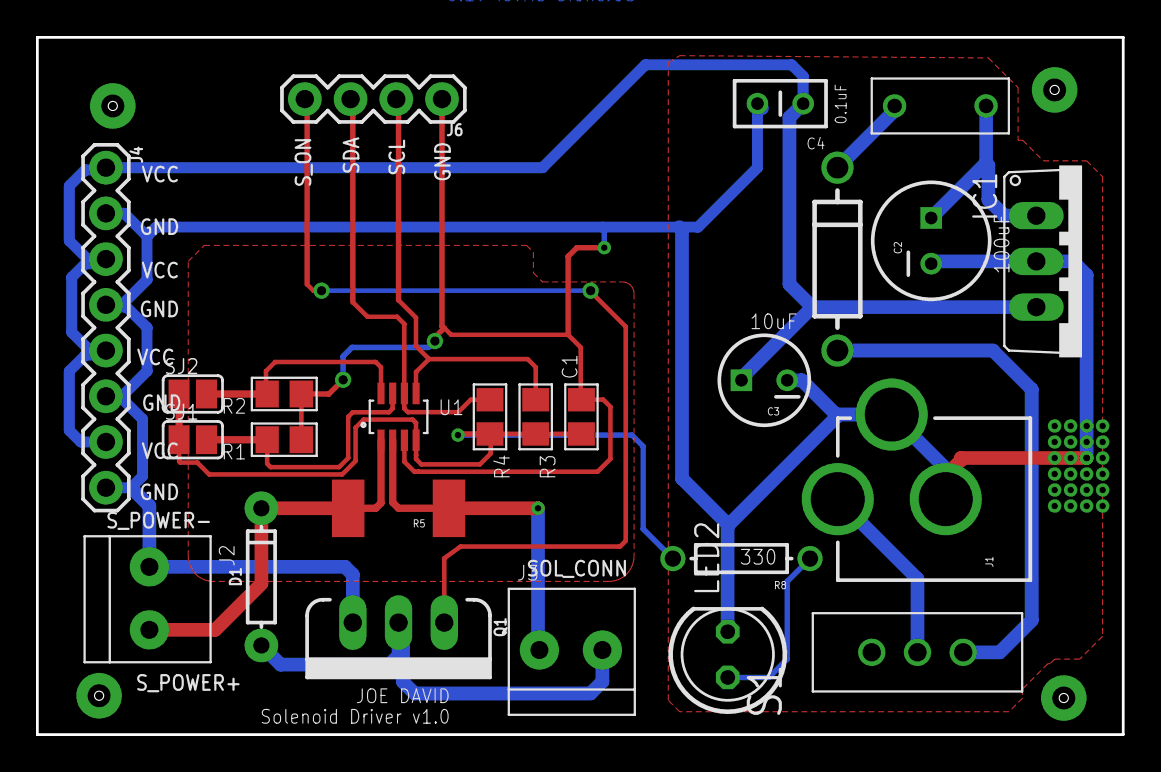
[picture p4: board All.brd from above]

Board: 2 copper layers, 60.3 x 38.7 mm, 25 parts (0 on the bottom side), 15 nets.

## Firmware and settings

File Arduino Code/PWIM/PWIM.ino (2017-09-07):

//------- CLASSES ------- //

#include <PID_v1.h>           // Class Definition for the PID Algorithm
#include <LiquidCrystal.h>    // Class Definition for the 16x4 LCD
#include <Wire.h>             // Class Definition to communicate via I2C with the sensor
#include <Adafruit_INA219.h>  // Class Definition for the Sensor


// ---- ARDUINO GPIO PINS ---- //

const int joystick = A0;      // analog pin used to connect the JOYSTICK
const int pwm = 9;            //pin to drive mosfet which in return drives the solenoid  

// ---- VARIABLES ---- //
 
float dutycycle;                // variable to read the duty cycle from joystick         
float amps;                     // variable to store the current
double Setpoint, Input, Output; //setpoint, input and output parameters of the controller
double Kp=0, Ki=10, Kd=0;       //Specify initial tuning parameters
int avg = 0;

// ------ CREATING OBJECTS OF CLASSES ------//

Adafruit_INA219 ina219;             // Object of Class Adafruit_INA219
LiquidCrystal lcd(12,11,5,4,3,2);   // Object Of Class LiquidCrystal

PID myPID(&Input, &Output, &Setpoint, Kp, Ki, Kd,P_ON_E,DIRECT);   // Object of Class PID


// ---- SETUP FUCNCTION ---- //

void setup() {
  
  #ifndef ESP8266
    while (!Serial);     // will pause Zero, Leonardo, etc until serial console opens
  #endif
  
  ina219.begin();       // Initialize first board (default address 0x40)

  // Setting LCD Parameters
  lcd.begin(16,4);
  lcd.clear();
  lcd.setCursor(0,0);
  lcd.print("Duty:");
  lcd.setCursor(9,0);
  lcd.print("V:");
  lcd.setCursor(0,1);
  lcd.print("I1:");
  lcd.setCursor(7,1);
  lcd.print("I2:");
  lcd.setCursor(14,1);
  lcd.print("mA");
  lcd.setCursor(0,2);
  lcd.print("Power: ");
  lcd.setCursor(15,2);
  lcd.print("W");
  lcd.setCursor(0,3);
  lcd.print("Kp:");
  lcd.setCursor(3,3);
  lcd.print((int)Kp);
  lcd.setCursor(5,3);
  lcd.print("Ki:");
  lcd.setCursor(9,3);
  lcd.print((int)Ki);
  lcd.setCursor(12,3);
  lcd.print("Kd:");
  lcd.setCursor(15,3);
  lcd.print((int)Kd);

  // Setting PID Parameters
  myPID.SetOutputLimits(0, 255);    //  set PWM output limit
  myPID.SetMode(AUTOMATIC);         //  Set PID mode as Automatic

  // Setting Arduino Parameters
  pinMode(pwm, OUTPUT);                 //Set PIN 9 as Output
  setPwmFrequency(9,2); // setting frequency to 3Khz
 // TCCR1A = _BV(COM1A1) | _BV(COM1B1) ; // phase and frequency correct mode. NON-inverted mode
 // TCCR1B = _BV(WGM13) | _BV(CS11);
  
  // Setting Serial Communication Parameters.
  Serial.begin(115200);
}


// ---- LOOP FUCNCTION ---- //

void loop() {
  // Variables
  int pwmspan;
  int Setpoint_;
  long int total = 0, total1 = 0;

  // Reading average Analog Input from Joystick
  for ( int i = 0; i < 100; i++)
  {
    total+= analogRead(joystick);
  }
  avg = total / 100;

  //Mappin the Input to PWM Value
  Setpoint=map(avg,0,1023, 0,255); // Setpoint is dutycycle (range 0-255

  // Reading average input from the current sensor
  for ( int i = 0; i < 100; i++)
  {
    total1+= ina219.getCurrent_mA();
  }
  amps = total1 / 100;

  if(amps<0)
  amps=0;
 
  Input = amps/950*255;  // current with all components on board taking into account
                        // the voltage drops across all componenets is 0.99A
  myPID.Compute();      // Computes the PID Output
  delay(1);             // 1 millisecond delay for PID Stability
  
  // Writing PID Computed Output (with Dither) to the Valve 
  analogWrite(pwm,Output);
 

  // Plotting the Setpoint Input and Output
  Serial.print(Setpoint);
  Serial.print(" ");
  Serial.print(Input);
  Serial.print(" ");
  Serial.println(Output);
  
  // Printing Relevant information in the LCD
  printlcd();

  delay(10);
}



void printlcd() {
  
  int duty_,e_curr_;
  char e_curr[5],duty[5],amps_[5];
  float shuntvoltage = 0;
  float busvoltage = 0;
  float loadvoltage = 0;
  float power=0;

  shuntvoltage = ina219.getShuntVoltage_mV();
  busvoltage = ina219.getBusVoltage_V();
  loadvoltage = busvoltage + (shuntvoltage / 1000);
  
  lcd.setCursor(4,0);
  duty_ = (float)avg/1023*100;

  snprintf(duty, 5, "%4d", duty_); // %4d = 4 digits, right aligned
  lcd.print(duty);

  lcd.setCursor(10,1);
  e_curr_ = (float)duty_/100.0 * 950;
  snprintf(e_curr, 5, "%4d", e_curr_); // %4d = 4 digits, right aligned
  lcd.print(e_curr);
  
  lcd.setCursor(3,1);
  lcd.print((int)amps);
  //delay(500);

   power = loadvoltage * amps/1000.0;
   
  lcd.setCursor(7,2);
  lcd.print(power);
  

 

  lcd.setCursor(11,0);
  lcd.print(loadvoltage);

}

void setPwmFrequency(int pin, int divisor) {
  byte mode;
  if(pin == 5 || pin == 6 || pin == 9 || pin == 10) {
    switch(divisor) {
      case 1: mode = 0x01; break;
      case 2: mode = 0x02; break;
      case 3: mode = 0x03; break;
      case 4: mode = 0x04; break;
      case 5: mode = 0x05; break;
      default: return;
    }
    if(pin == 5 || pin == 6) {
      TCCR0B = TCCR0B & 0b11111000 | mode;
    } else {
      TCCR1B = TCCR1B & 0b11111000 | mode;
    }
  } else if(pin == 3 || pin == 11) {
    switch(divisor) {
      case 1: mode = 0x01; break;
      case 2: mode = 0x02; break;
      case 3: mode = 0x03; break;
      case 4: mode = 0x04; break;
      case 5: mode = 0x05; break;
      case 6: mode = 0x06; break;
      case 7: mode = 0x07; break;
      default: return;
    }
    TCCR2B = TCCR2B & 0b11111000 | mode;

}}

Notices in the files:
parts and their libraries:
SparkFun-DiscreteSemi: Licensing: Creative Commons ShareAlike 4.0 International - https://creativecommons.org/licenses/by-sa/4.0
